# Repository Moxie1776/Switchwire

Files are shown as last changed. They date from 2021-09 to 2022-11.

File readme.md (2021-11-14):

# Voron Switchwire

<!-- ![Switchwire](./images/SWbedOn.jpg)  -->

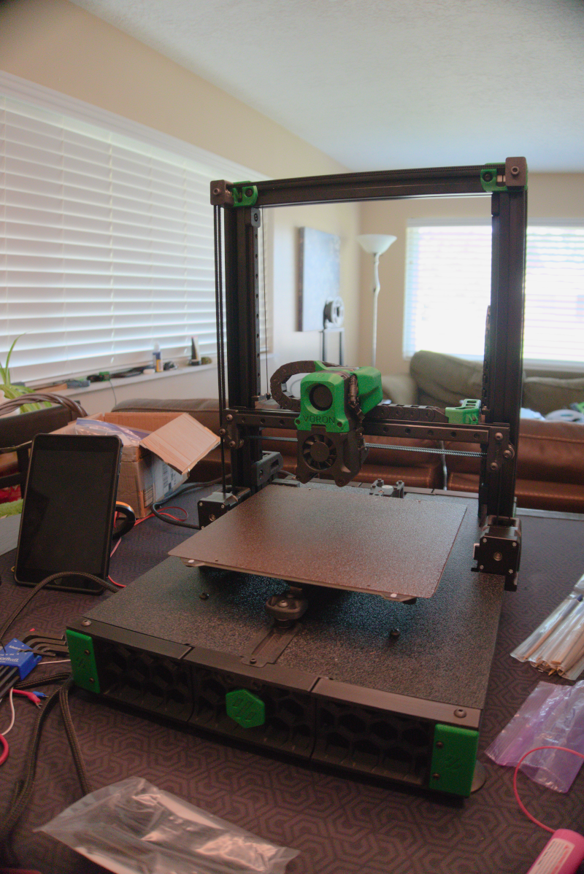
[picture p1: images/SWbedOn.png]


### BOM

-   Includes tax and S&H as much as was feasible
-   Due to my on hand parts some parts from the original BOM are not included

##### Printed Parts

-   Black Inland ABS
-   Green [KVP ABS](https://www.villageplastics.com/product/abs/)
-   printed FB friend (for a price)    
-   Black with Green accents

##### Fastners

-   [Fysetc Switchwire Fastner Set](https://www.aliexpress.com/item/1005002965204693.html) $37.66

##### Motion

-   [FYSETC GT2 Timing Belt](https://www.amazon.com/gp/product/B07BRKZGMS) $10.88
    -   [GATES-LL-2GT-6 Synchronous GT2](https://www.aliexpress.com/item/4001230715938.html) $31.79
    -   I have these on hand ready to put on
-   [POWGE 20 teeth 2GT Pulley Black Anodizing](https://www.aliexpress.com/item/4000454459268.html) $16.14
-   [Mellow F695-2RS Bearing 5_13_4 mm Flanged Bushing x2](https://www.aliexpress.com/item/1005001315513956.html) $20.38
-   [RobotDigg Black Anodized Linear Rails](https://www.robotdigg.com/product/1314/Black-anodized-linear-rail-7,-9,-12-and-15) $73.00
-   [Key-Bak](https://www.amazon.com/gp/product/B0088MQA10) $12.64

##### Vibration Management

-   [4 Rubber Compressor Feet](https://www.amazon.com/uxcell-47mmx18mm-Compressor-Replacement-Black/dp/B0711Y6T56) $9.99

##### Electronics

-   [Limit Switches](https://www.digikey.com/en/products/detail/omron-electronics-inc-emc-div/D2F-5L/8593137) $17.58
-   [Omron Proximity Switch Inductive Sensor 3 Wire](https://www.aliexpress.com/item/32442790824.html) $18.78
-   Bat-85 Diode not needed with the Fysetc S6
-   [Mean Well RS-25-5](https://www.digikey.com/en/products/detail/RS-25-5/1866-4145-ND/7706180) $11.54 ($4.99 S&H)
-   [NEMA17 Motor 17HS15-1504S-X1 x3](https://www.amazon.com/gp/product/B07LCK19D5) $30.22
-   [NEMA17 Motor 17HS08-1004S x3](https://www.amazon.com/gp/product/B00PNEQ79Q) $11.79
-   Mean Well LRS-350-24 PSU - recycled from Ender 3

-   [Filtered Power Inlet](https://www.amazon.com/gp/product/B081VD1NNT) $11.79
-   [40x40x10 Axial Fan 24V](https://www.aliexpress.com/item/32815685199.html) $4.65
-   [40x40x20 Blower Fan 24V](https://www.aliexpress.com/item/4001246935816.html) $5.06
-   60x60x20 Axial Fan (24V) - recycled from Ender 3 (upgraded PSU fan from original PSU)
-   [Raspberry Pi 4 Model B/4GB](https://www.pishop.us/product/raspberry-pi-4-model-b-4gb/) - recycled from Ender 3
-   [Fysetc S6 V2](https://www.aliexpress.com/item/4000345369228.html)
    -   [Fysetc TMC2209 v3.1 x 5](https://www.aliexpress.com/item/33025556705.html)

##### Frame

-   [LDO Frame](https://www.printedsolid.com/products/ldo-voron-switchwire-frame-kit) $95.00

##### Misc

-   [Neodymium Rare Earth Magnets 6x3mm 70pcs, Black](https://www.amazon.com/gp/product/B00HA2LM30) $16.99
-   [Mellow BMG Extruder Kit](https://www.aliexpress.com/item/1005002254569027.html) $25.61
-   [Mellow All Metal NF V6-Crazy Voron Hotend E3d V6](https://www.aliexpress.com/item/4001230851527.html) $33.67
-   [ Hook Up Wire, 24 AWG, Stranded Kit](https://www.remingtonindustries.com/hook-up-wire/custom-hook-up-wire-24-awg-stranded-kit-25-length-each-choose-6-colors/) $22.82
-   [10\*11mm Mini Nylon Drag Chain](https://www.aliexpress.com/item/33000014666.html) $19.99

##### Panels/Build Plate

-   [Prusa i3 MK3S Y carriage compatible with Voron Switchwire](https://www.aliexpress.com/item/4000046376872.html) $31.96
-   [Prusa I3 MK3 MK52 Heated Bed + Double Sided Textured Powder Coated PEI Spring Steel Sheet For VORON SW](https://www.aliexpress.com/item/4000016762364.html) $61.73
-   [Laser Cut ABS Deck, Enclosure (minus clear)](https://mnlasercutting.com/shop/voron-switchwire) $45.00
-   [Clear Acrylic Enclosure Parts](https://www.printedsolid.com/products/voron-switchwire-panel-set-made-from-aluminum-composite-material) $34.00
    -   I would have just purchased the entire enclosure set from printedsolid 'had a known'

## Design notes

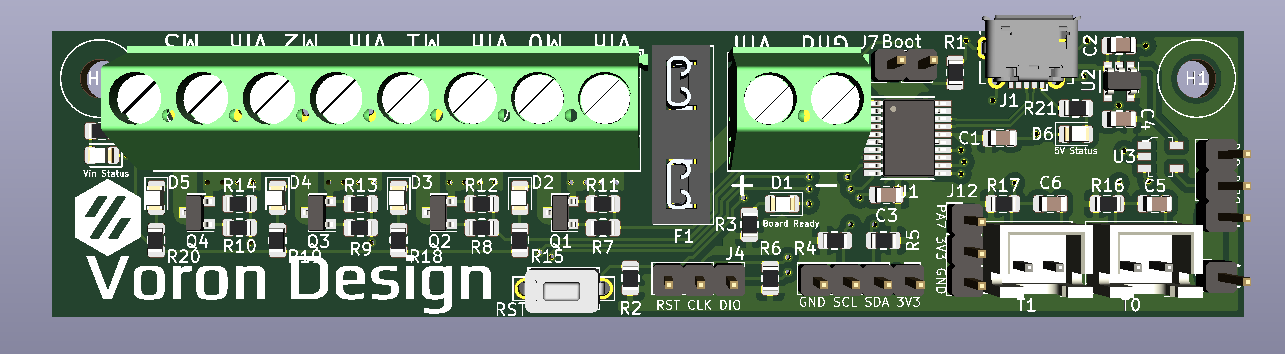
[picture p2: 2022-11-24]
electronics/Klipper_Expander/Images/STM32_Klipper_Expander.png

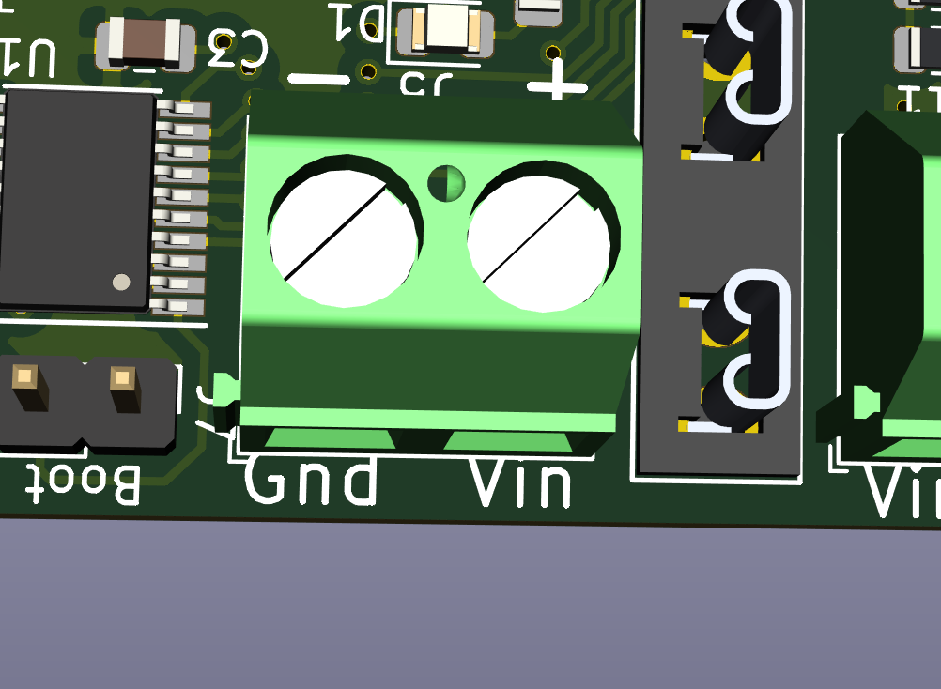
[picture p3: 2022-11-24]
electronics/Klipper_Expander/Images/Vin.png

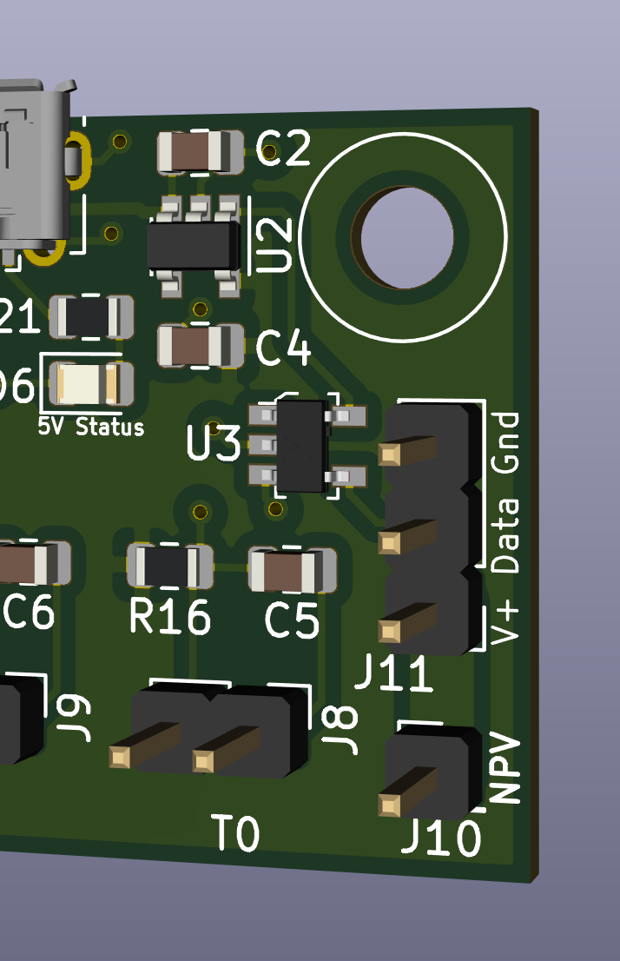
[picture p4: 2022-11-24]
electronics/Klipper_Expander/Images/Neopixel.png

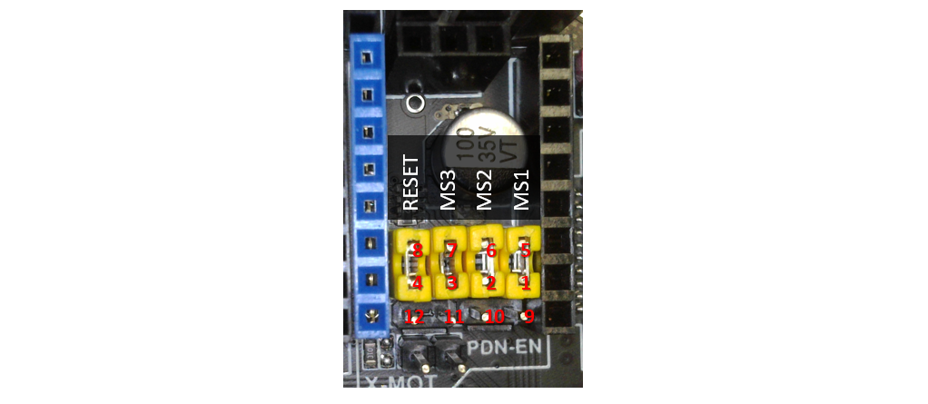
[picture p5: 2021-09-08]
electronics/FYSETC-S6-main/images/S6_1574477723736.png

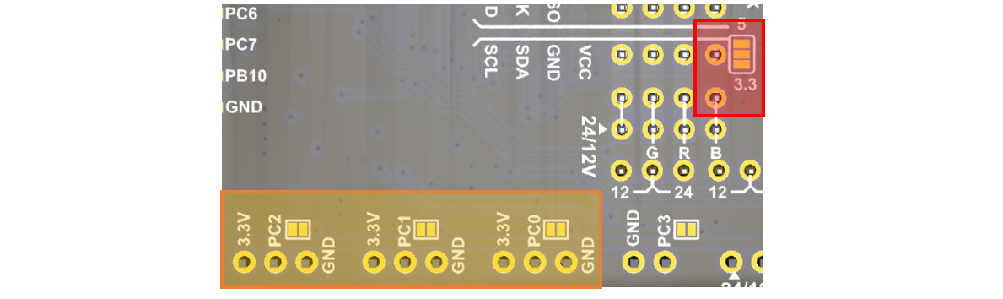
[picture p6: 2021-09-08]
electronics/FYSETC-S6-main/images/S6_1574476533464.png

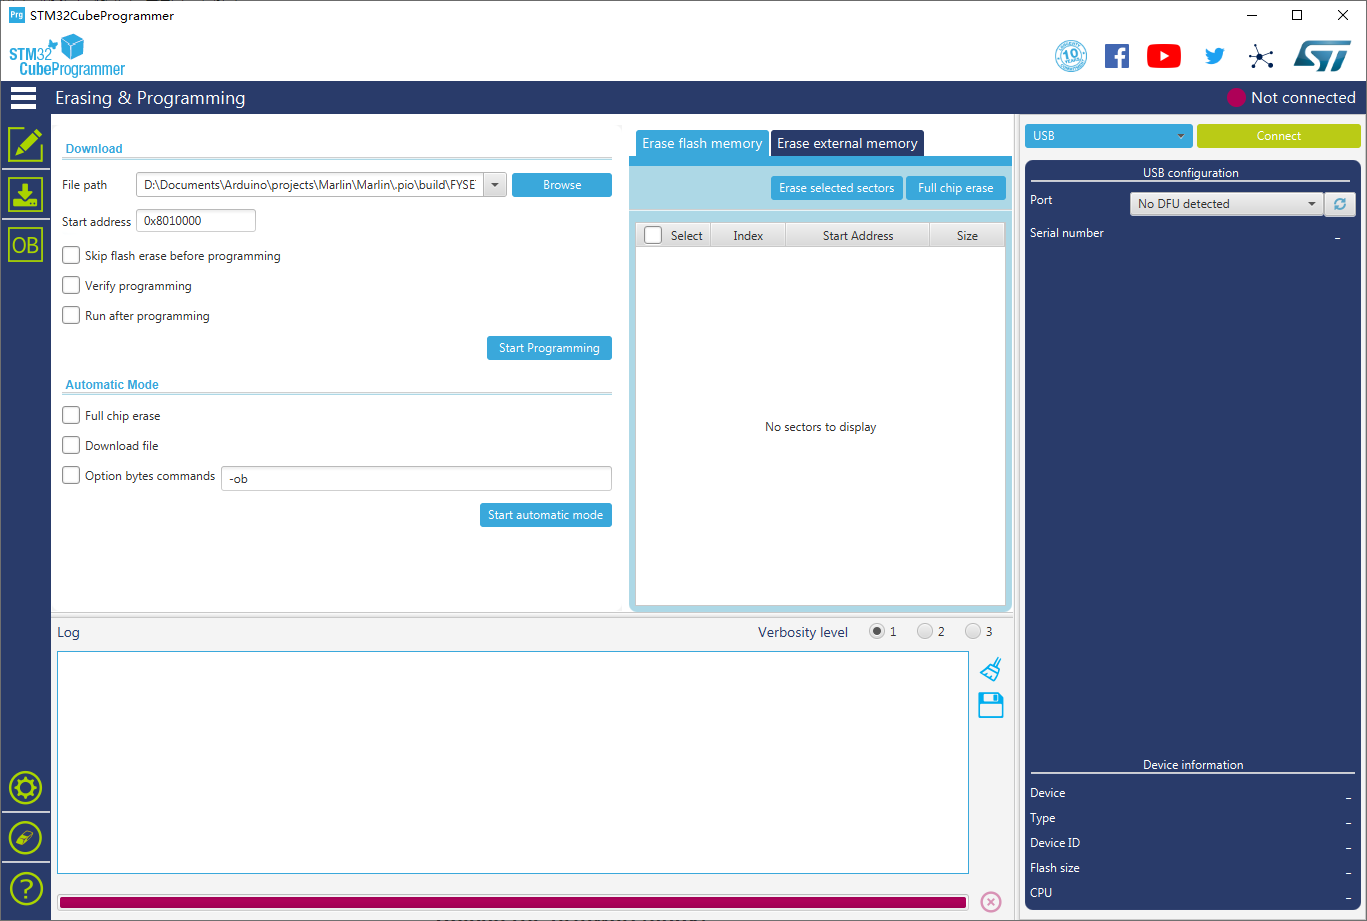
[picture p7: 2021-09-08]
electronics/FYSETC-S6-main/bootloader/images/STM32CubeProgrammer.png

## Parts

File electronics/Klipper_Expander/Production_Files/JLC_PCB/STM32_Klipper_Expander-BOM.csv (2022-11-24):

Comment | Designator | Footprint | LCSC
0.1uF | C1,C3 | KlipperExpander:C_0805_2012Metric | C49678
4.7uF | C4,C2,C5,C6 | KlipperExpander:C_0805_2012Metric | C1779
LED | D1,D2,D4,D3,D5,D7,D6 | KlipperExpander:LED_0805_2012Metric | C84256
Fuse | F1 | KlipperExpander:3544-2_FuseHolder
MountingHole | H1,H2 | KlipperExpander:MountingHole_3.2mm_M3
USB_B_Micro | J1 | KlipperExpander:Molex-105017-0001-USBMicroB
Conn_01x01 | J10 | KlipperExpander:PinHeader_1x01_P2.54mm_Vertical
Conn_01x03 | J11,J12,J4 | KlipperExpander:PinHeader_1x03_P2.54mm_Vertical
Conn_01x04 | J2 | KlipperExpander:PinHeader_1x04_P2.54mm_Vertical
Vin | J5 | KlipperExpander:1x02_ScrewTerminal_Phoenix
Screw_Terminal_01x08 | J6 | KlipperExpander:1x08_ScrewTerminal_Phoenix
Conn_01x02 | J7,J8,J9 | KlipperExpander:PinHeader_1x02_P2.54mm_Vertical
IRLML6344TRPBF | Q1,Q3,Q2,Q4 | KlipperExpander:SOT-23 | C20917
10K | R2,R1,R13,R12,R11,R6,R14 | KlipperExpander:R_0805_2012Metric | C17414
1K | R3,R21 | KlipperExpander:R_0805_2012Metric | C17513
4.7K | R5,R4,R15,R19,R18,R20,R22,R16,R17 | KlipperExpander:R_0805_2012Metric | C17673
100 | R7,R8,R9,R10 | KlipperExpander:R_0805_2012Metric | C17408
SW_SPST | SW2 | KlipperExpander:2PinTactileButton
STM32F042F6Px | U1 | KlipperExpander:TSSOP-20_4.4x6.5mm_P0.65mm | C81000
AP2127K-3.3 | U2 | KlipperExpander:SOT-23-5 | C156285
74LVC1G17 | U3 | KlipperExpander:SOT-753 | C6076

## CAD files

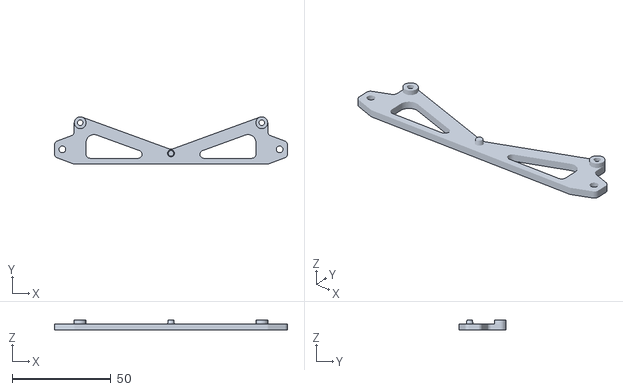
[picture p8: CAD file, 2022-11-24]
electronics/Klipper_Expander/CAD/KlipperExpander_HorizontalMount.STL
118.0 x 24.0 x 5.00

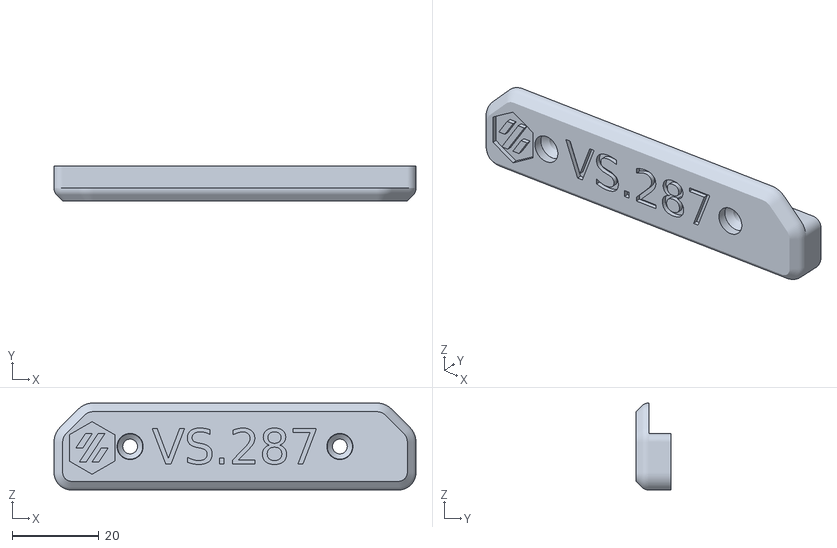
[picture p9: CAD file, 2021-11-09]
serialFiles/VS.287.stl
83.2 x 8.00 x 20.0

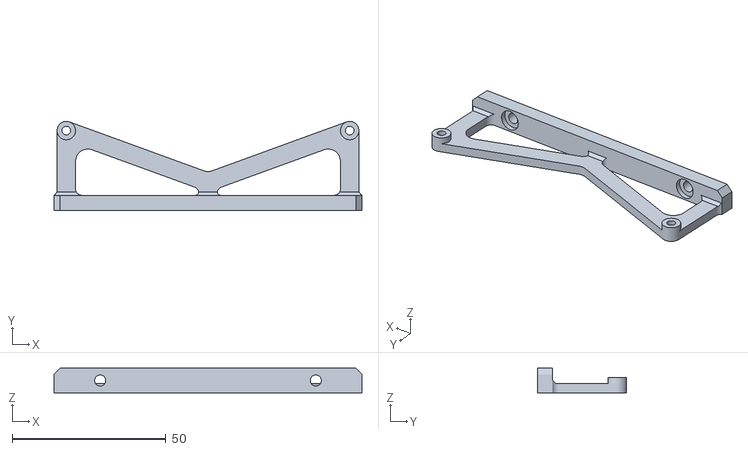
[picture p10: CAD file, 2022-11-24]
electronics/Klipper_Expander/CAD/KlipperExpander_VerticalMount.STL
100.0 x 29.0 x 8.00

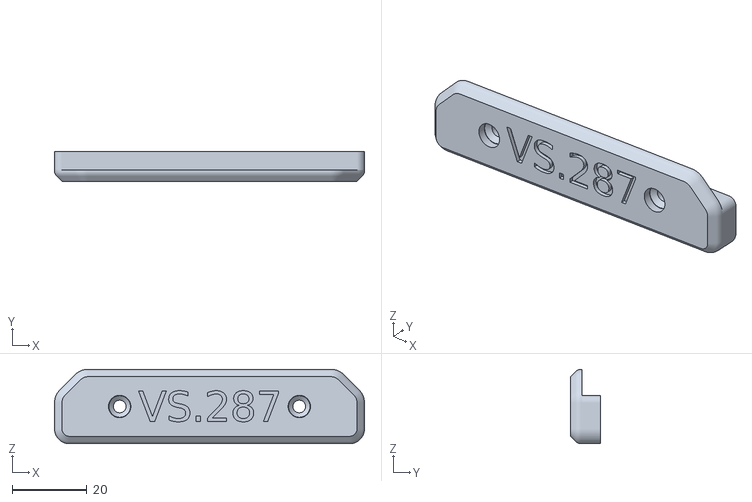
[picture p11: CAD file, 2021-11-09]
serialFiles/VS.287-NoLogo.stl
83.2 x 8.00 x 20.0

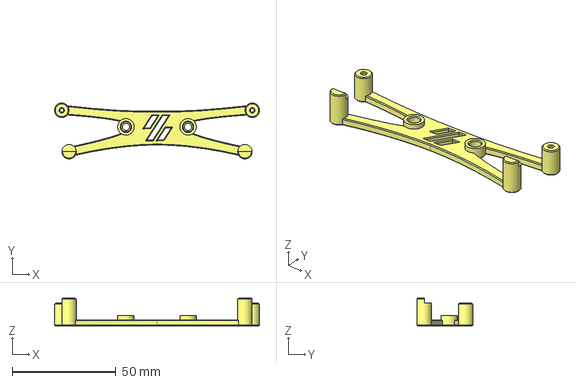
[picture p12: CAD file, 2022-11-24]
electronics/Klipper_Expander/CAD/KlipperExpander_RailMount.step
99.0 x 27.0 x 13.5 mm

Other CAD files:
electronics/Klipper_Expander/CAD/KlipperExpander_RailMount.stl

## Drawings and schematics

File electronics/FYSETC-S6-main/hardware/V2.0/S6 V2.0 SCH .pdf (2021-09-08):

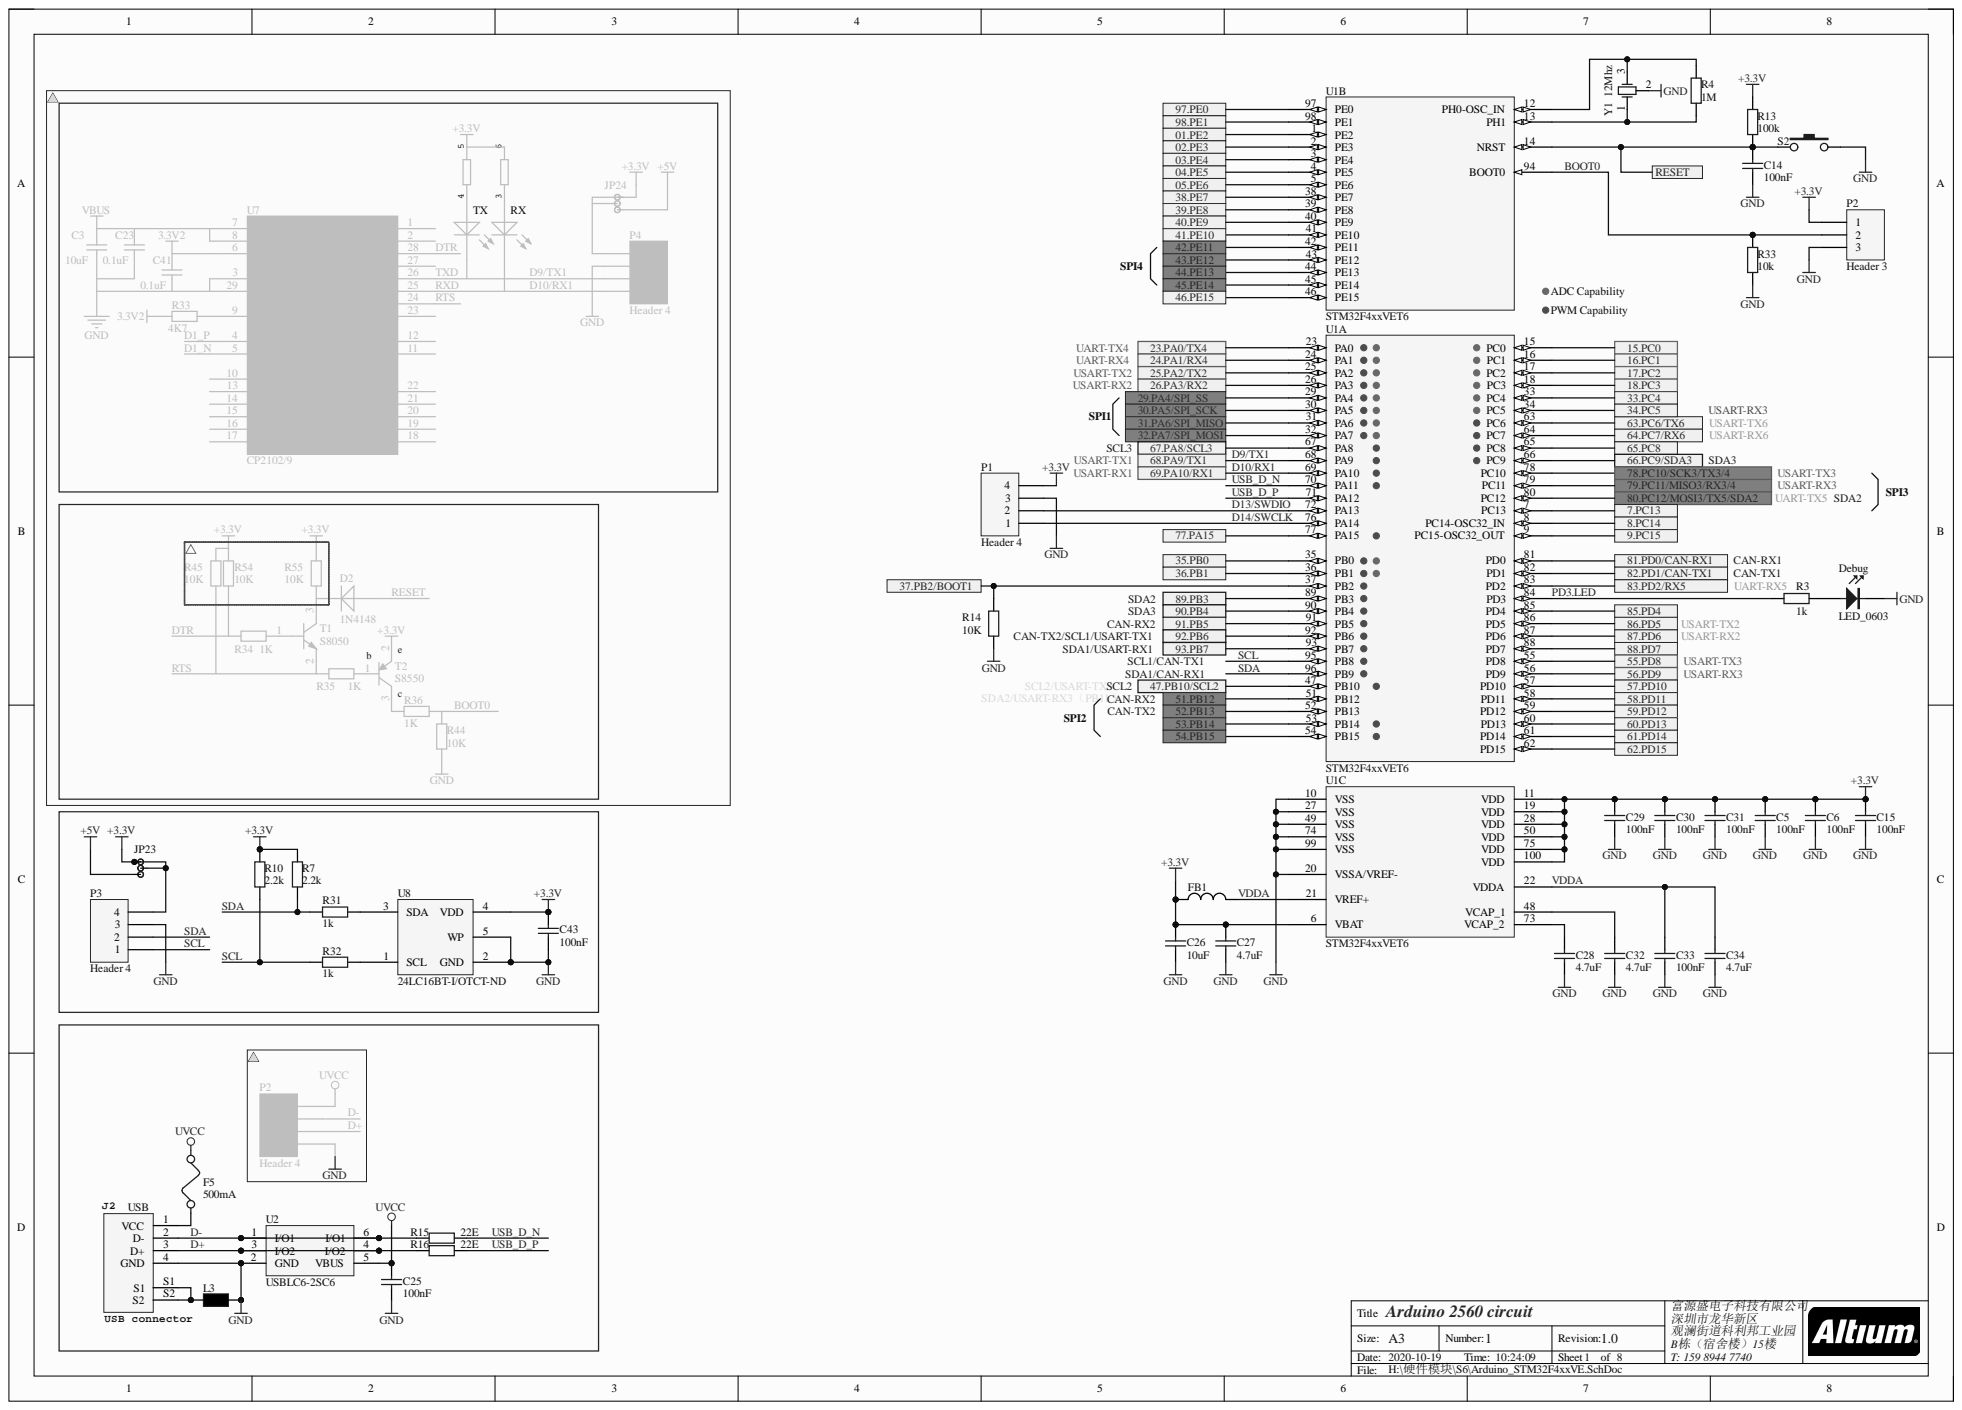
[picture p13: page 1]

01.PE2 | PE2 1
02.PE3 | PE4 3 | BOOT0

05.PE6 | PE7 38
38.PE7 | PE8 39

32.PA7/SPI_MOSI | | 64.PC7/RX6
67.PA8/SCL3 | PA8 67 | 65.PC8

35.PB0 | | PB1 36 | | 81.PD0/CAN-RX1
36.PB1 | | | | 82.PD1/CAN-TX1

89.PB3 | PB4 90
91.PB5 | | PB5 91 | | 86.PD5
92.PB6 | | PB6 92 | | 87.PD6
93.PB7 | SCL | PB8 95 | | 88.PD7

47.PB10/SCL2 | PB12 51 | 57.PD10
51.PB12 | PB13 52 | 58.PD11
52.PB13 | | 59.PD12
53.PB14 | PB14 53 | 60.PD13
54.PB15 | | 61.PD14

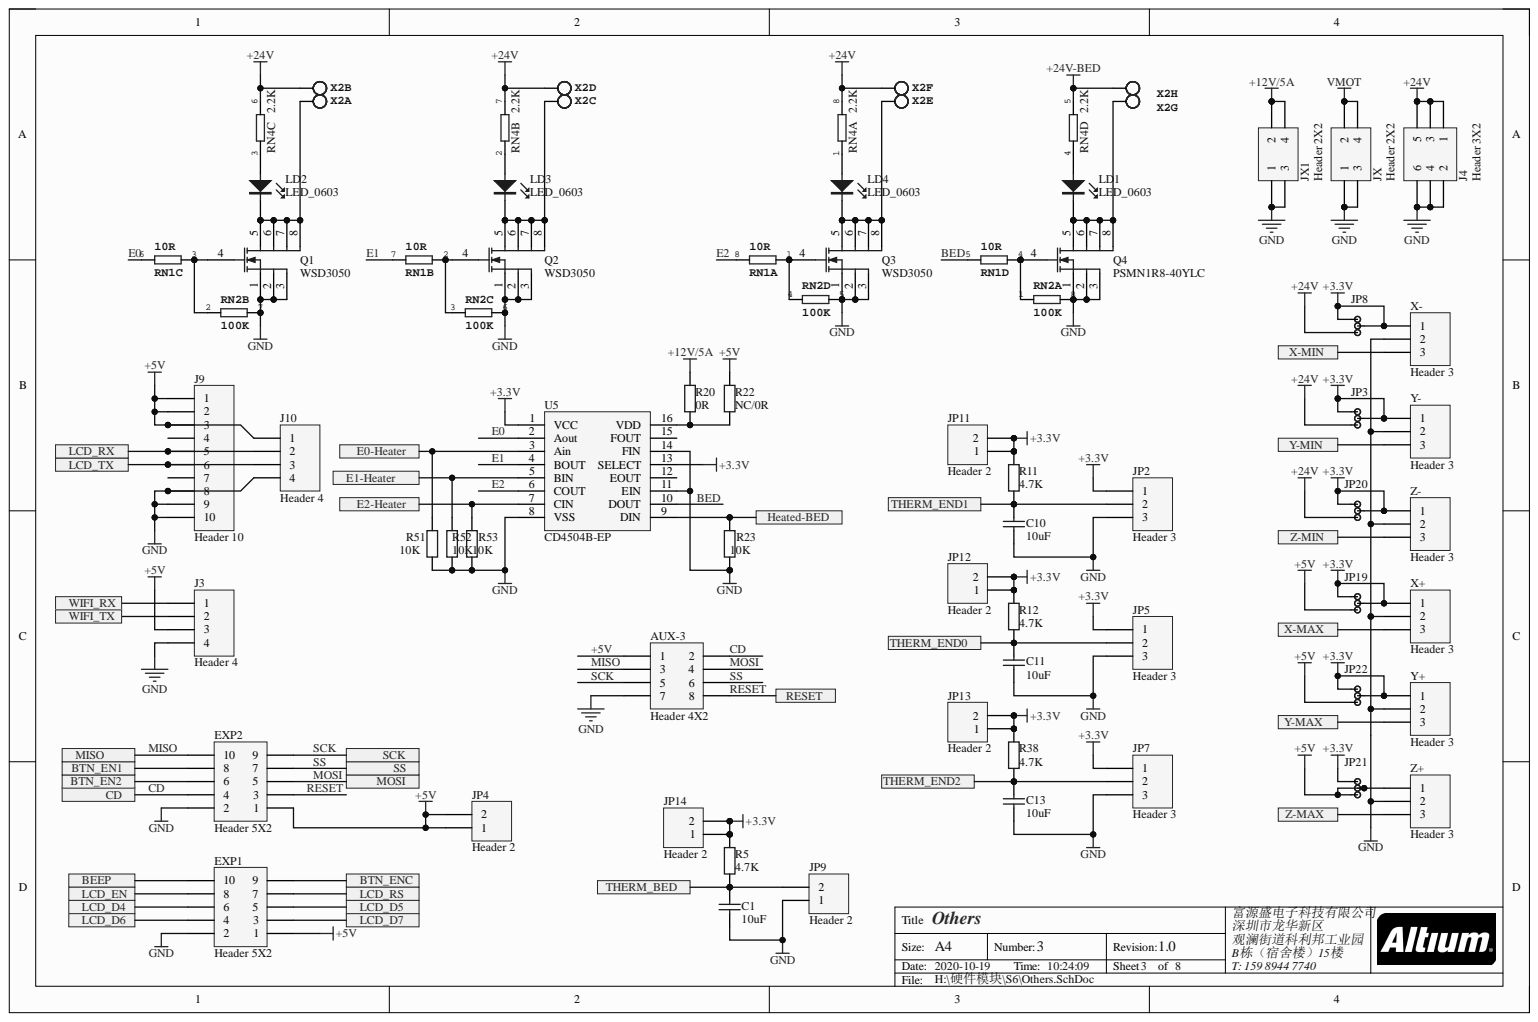
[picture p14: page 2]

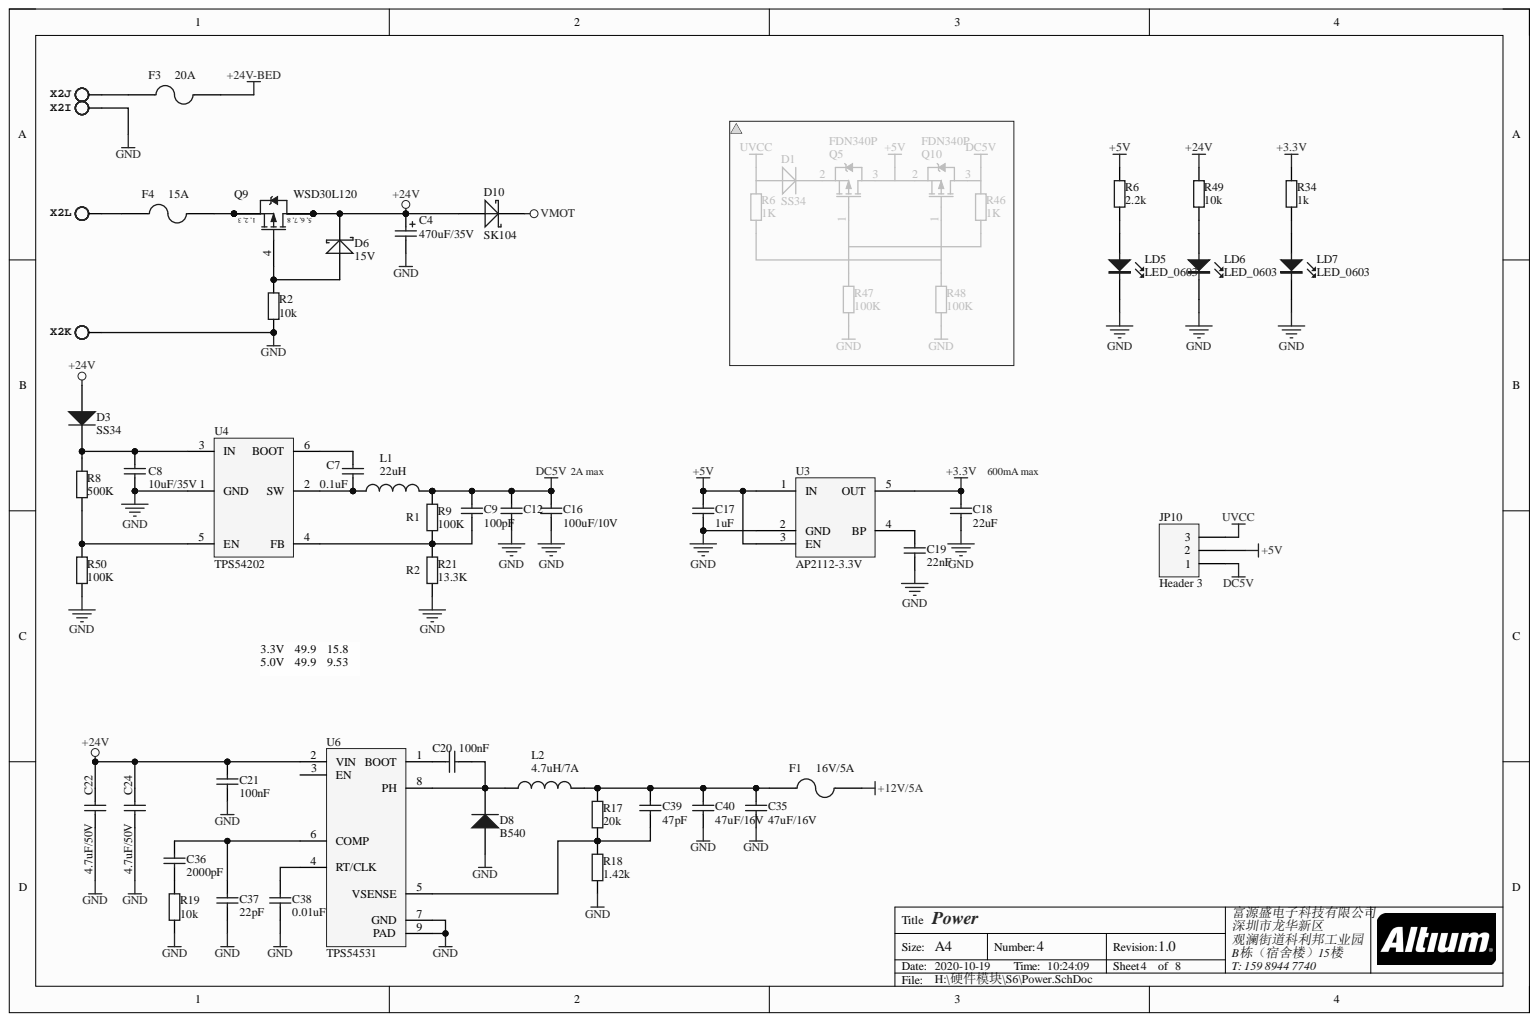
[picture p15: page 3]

RT/CLK 4

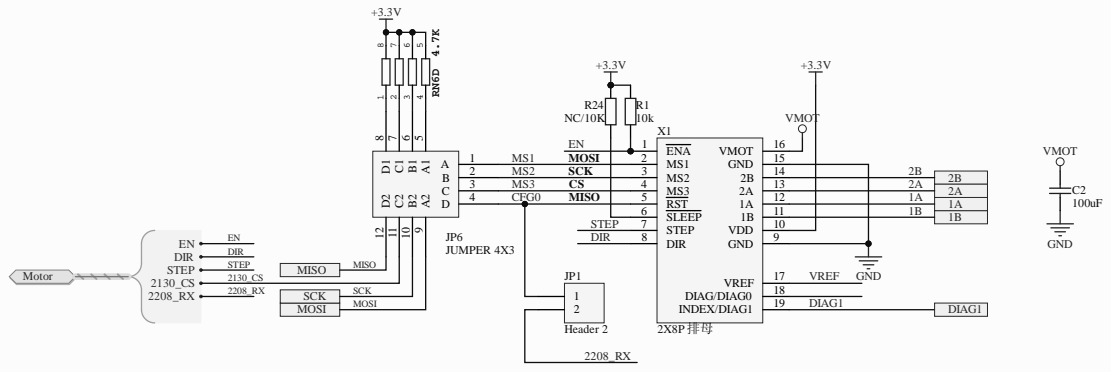
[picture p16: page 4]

2 MS2 SC K | 3 | 1 4
3 MS3 C S | 4 | 1 3 | | 2 A
4 CFG 0 ISO M | 5 | 1 2 | | 1 A

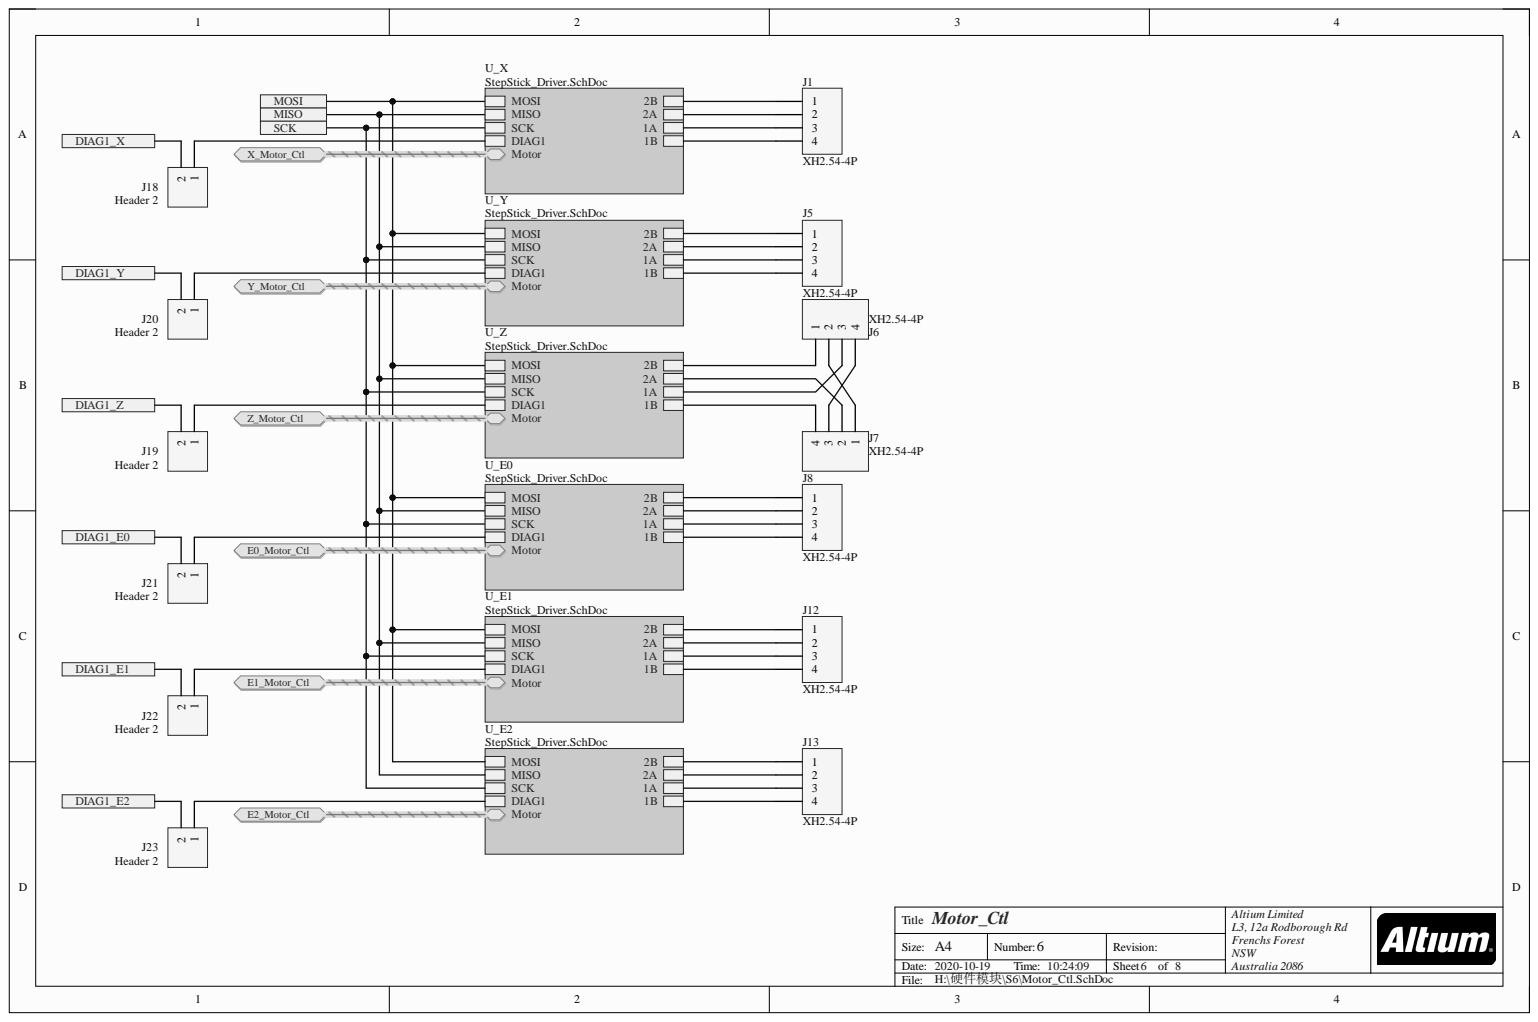
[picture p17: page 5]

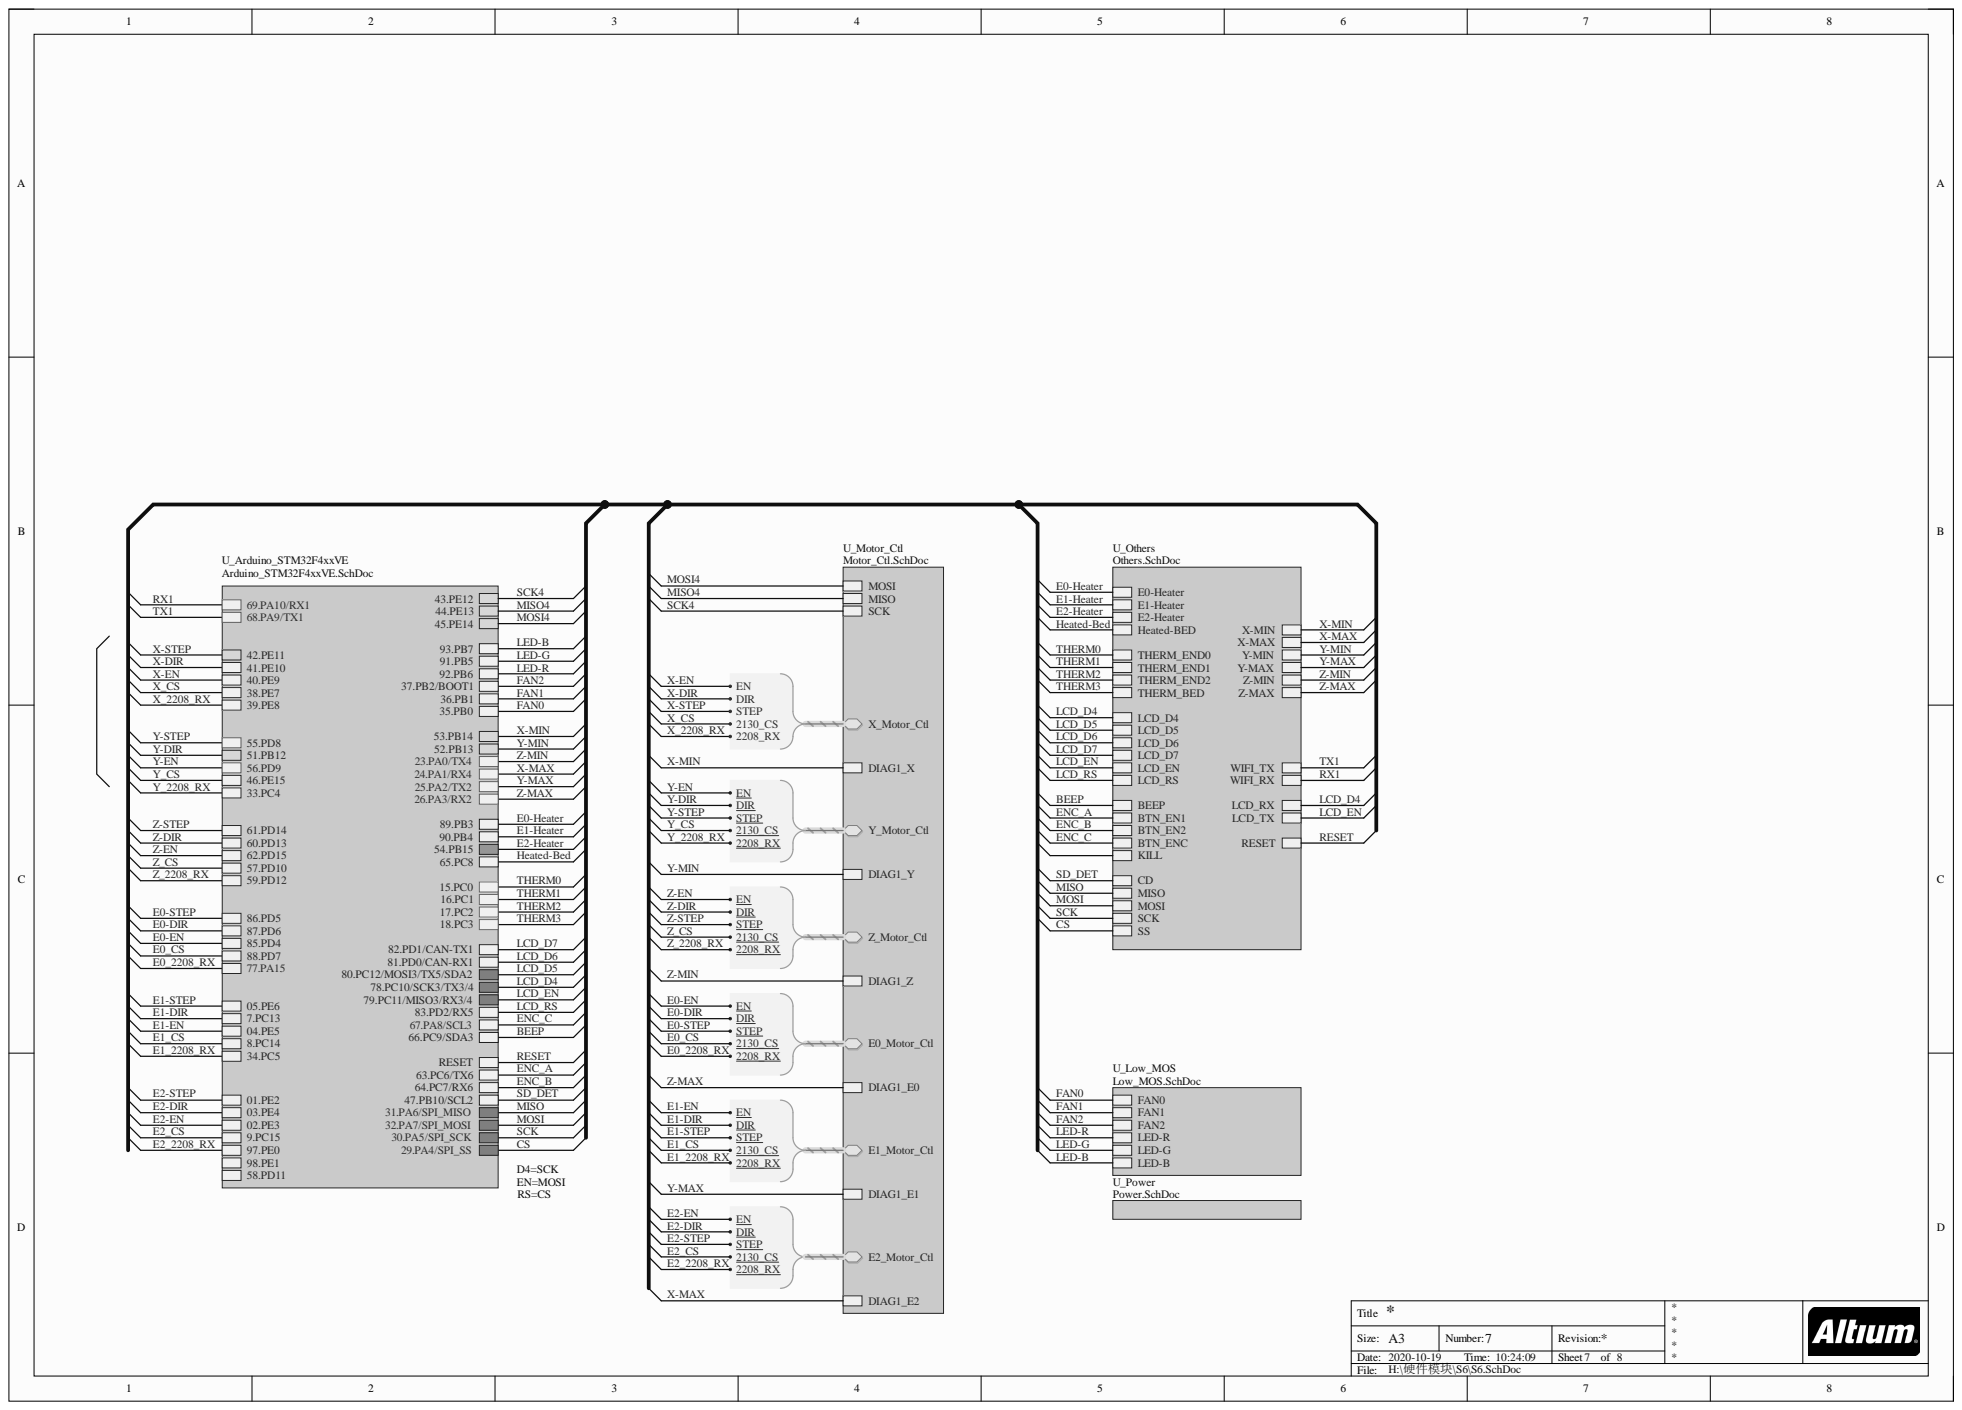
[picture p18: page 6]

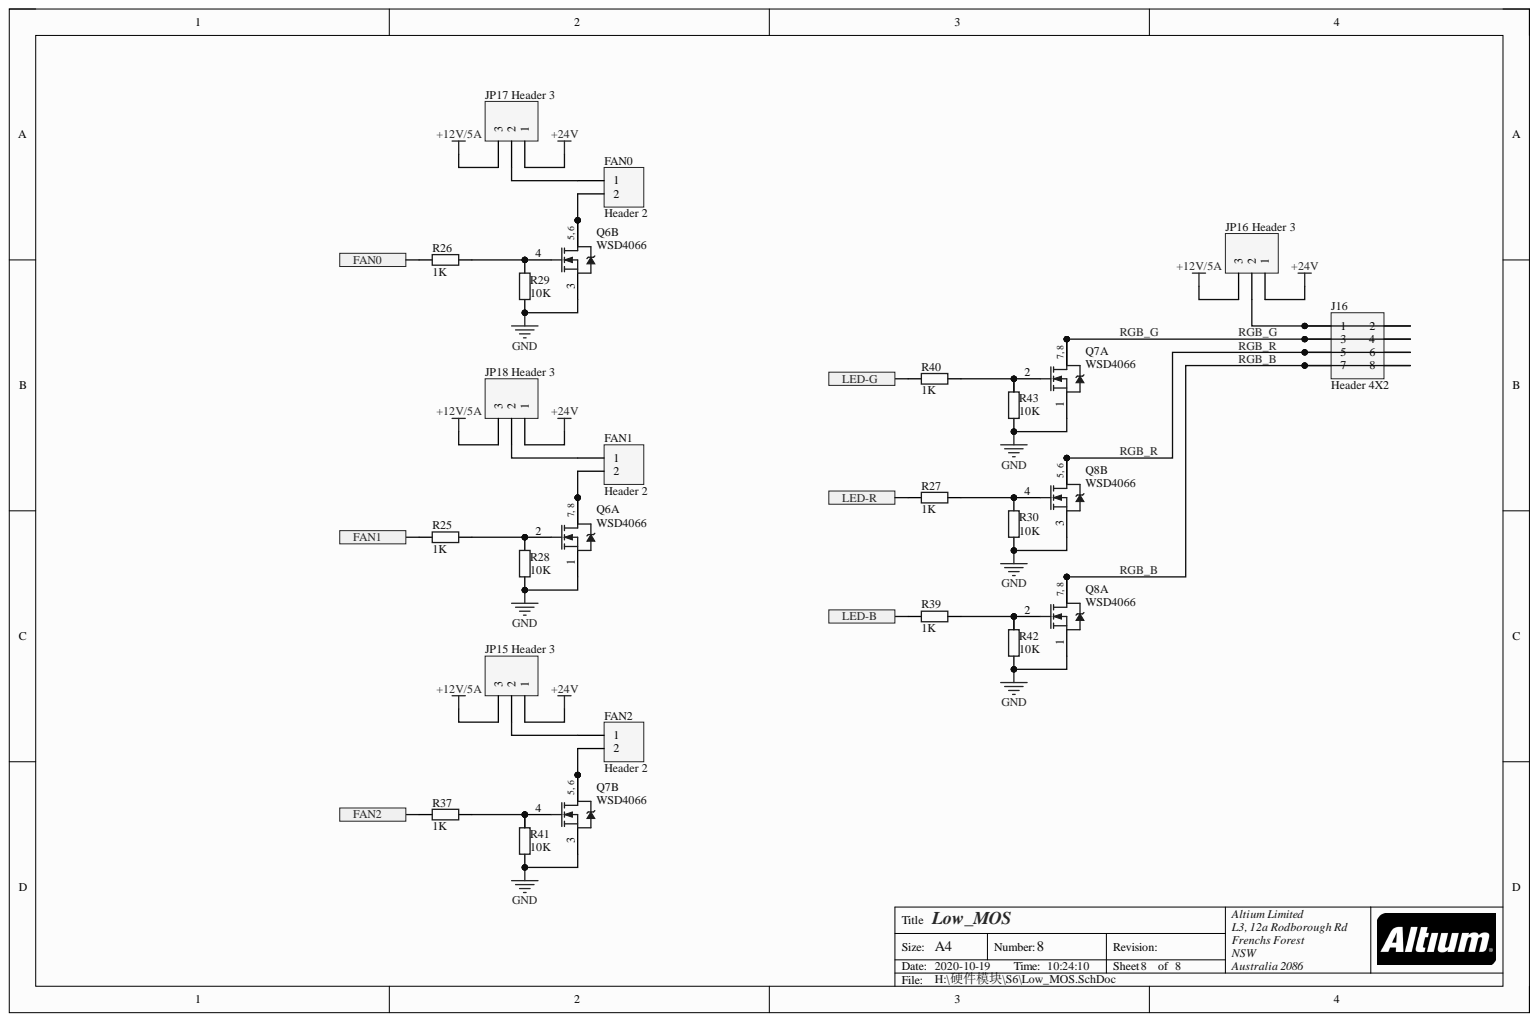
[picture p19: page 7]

RGB_ R Q 7 A | 5 6

RGB_ B | 7 8

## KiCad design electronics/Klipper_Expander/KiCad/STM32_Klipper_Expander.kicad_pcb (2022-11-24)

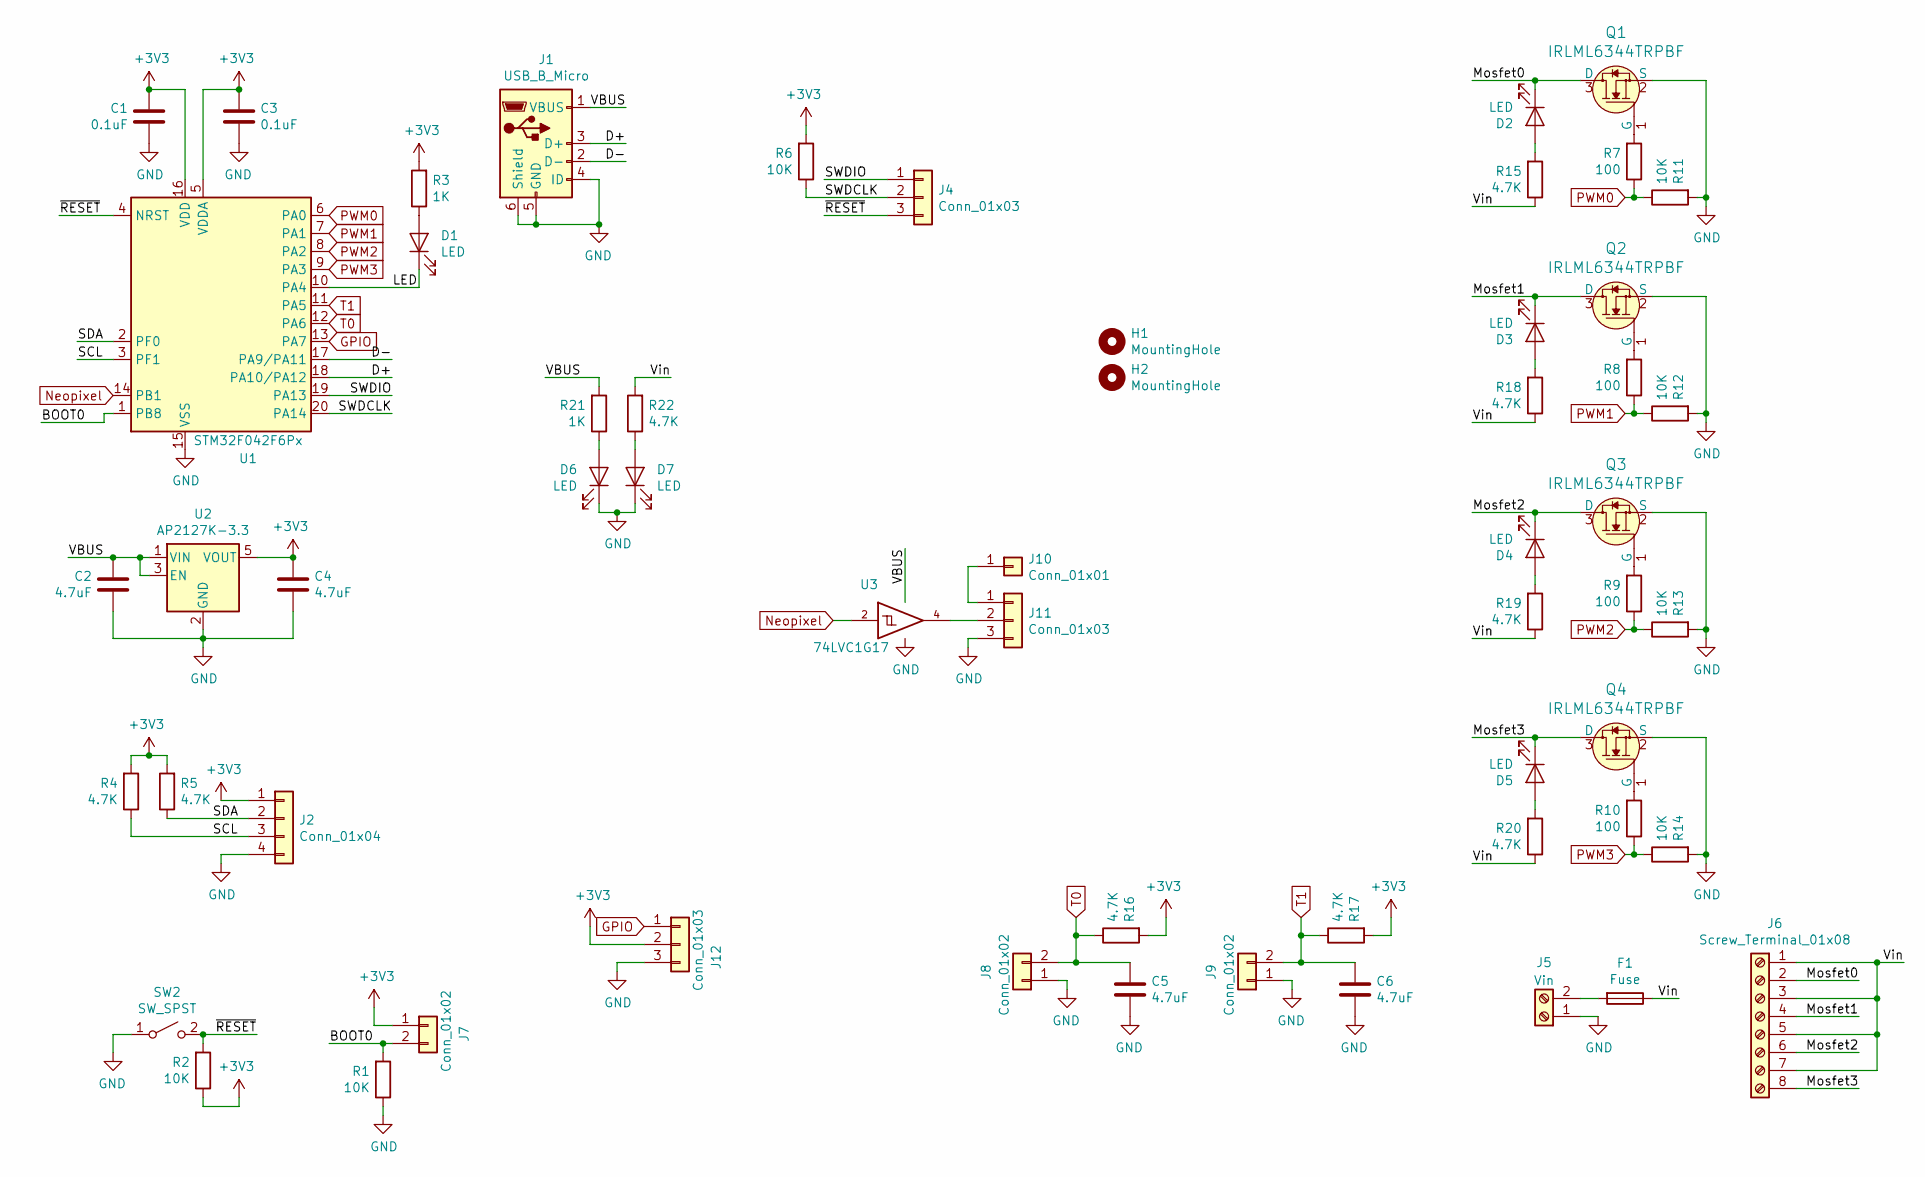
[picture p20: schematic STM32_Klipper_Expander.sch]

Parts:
C1, C3: 0.1uF; C_0805_2012Metric; MPN CC0805KRX7R9BB104; LCSC C49678
C2, C4, C5, C6: 4.7uF; C_0805_2012Metric; MPN CC0805KKX5R8BB475; LCSC C1779
D1, D2, D3, D4, D5, D6, D7: LED; LED_0805_2012Metric; MPN 17-215SURC/S530-A2/TR8; LCSC C84256
F1: Fuse; 3544-2_FuseHolder
H1, H2: MountingHole; MountingHole_3.2mm_M3
J1: USB_B_Micro; Molex-105017-0001-USBMicroB; MPN 1050170001
J2: Conn_01x04; PinHeader_1x04_P2.54mm_Vertical
J4, J11, J12: Conn_01x03; PinHeader_1x03_P2.54mm_Vertical
J5: Vin; 1x02_ScrewTerminal_Phoenix
J6: Screw_Terminal_01x08; 1x08_ScrewTerminal_Phoenix
J7, J8, J9: Conn_01x02; PinHeader_1x02_P2.54mm_Vertical
J10: Conn_01x01; PinHeader_1x01_P2.54mm_Vertical
Q1, Q2, Q3, Q4: IRLML6344TRPBF; SOT-23; MPN IRLML6344TRPBF; Digi-Key_PN IRLML6344TRPBFCT-ND
R1, R2, R6, R11, R12, R13, R14: 10K; R_0805_2012Metric; MPN RC0805JR-0710KL; LCSC C17414
R3, R21: 1K; R_0805_2012Metric; MPN RC0805JR-071KL; LCSC C17513
R4, R5, R15, R16, R17, R18, R19, R20, R22: 4.7K; R_0805_2012Metric; MPN RC0805JR-074K7L; LCSC C17673
R7, R8, R9, R10: 100; R_0805_2012Metric; MPN RC0805JR-07100RL; LCSC C17408
SW2: SW_SPST; 2PinTactileButton
U1: STM32F042F6Px; TSSOP-20_4.4x6.5mm_P0.65mm; MPN STM32F042F6P6; LCSC C81000
U2: AP2127K-3.3; SOT-23-5; MPN AP2127K-3.3TRG1; LCSC C156285
U3: 74LVC1G17; SOT-753; LCSC C6076

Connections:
+3V3: C1.2, C3.2, C4.2, J2.1, J7.1, J12.2, R2.1, R3.2, R4.2, R5.2, R6.2, R16.2, R17.2, U1.5 (VDDA), U1.16 (VDD), U2.5 (VOUT)
/BOOT0: J7.2, R1.2, U1.1 (PB8)
/D+: J1.3 (D+), U1.18 (PA10/PA12)
/D-: J1.2 (D-), U1.17 (PA9/PA11)
/LED: D1.1 (K), U1.10 (PA4)
/Mosfet0: D2.1 (K), J6.2, Q1.3 (D)
/Mosfet1: D3.1 (K), J6.4, Q2.3 (D)
/Mosfet2: D4.1 (K), J6.6, Q3.3 (D)
/Mosfet3: D5.1 (K), J6.8, Q4.3 (D)
/SCL: J2.3, R4.1, U1.3 (PF1)
/SDA: J2.2, R5.1, U1.2 (PF0)
/SWDCLK: J4.2, R6.1, U1.20 (PA14)
/SWDIO: J4.1, U1.19 (PA13)
/Vin: F1.1, J6.1, J6.3, J6.5, J6.7, R15.1, R18.1, R19.1, R20.1, R22.2
/~RESET: J4.3, R2.2, SW2.2 (B), U1.4 (NRST)
GND: C1.1, C2.1, C3.1, C4.1, C5.1, C6.1, D6.1 (K), D7.1 (K), J1.4 (ID), J1.5 (GND), J1.6 (Shield), J2.4, J5.1, J8.1, J9.1, J11.3, J12.3, Q1.2 (S), Q2.2 (S), Q3.2 (S), Q4.2 (S), R1.1, R11.2, R12.2, R13.2, R14.2, SW2.1 (A), U1.15 (VSS), U2.2 (GND), U3.3 (GND)
GPIO: J12.1, U1.13 (PA7)
Neopixel: U1.14 (PB1), U3.2
unnamed: D1.2 (A), R3.1
unnamed: D2.2 (A), R15.2
unnamed: D3.2 (A), R18.2
unnamed: D4.2 (A), R19.2
unnamed: D5.2 (A), R20.2
unnamed: D6.2 (A), R21.1
unnamed: D7.2 (A), R22.1
unnamed: F1.2, J5.2
unnamed: J10.1, J11.1
unnamed: J11.2, U3.4
unnamed: Q1.1 (G), R7.2
unnamed: Q2.1 (G), R8.2
unnamed: Q3.1 (G), R9.2
unnamed: Q4.1 (G), R10.2
PWM0: R7.1, R11.1, U1.6 (PA0)
PWM1: R8.1, R12.1, U1.7 (PA1)
PWM2: R9.1, R13.1, U1.8 (PA2)
PWM3: R10.1, R14.1, U1.9 (PA3)
T0: C5.2, J8.2, R16.1, U1.12 (PA6)
T1: C6.2, J9.2, R17.1, U1.11 (PA5)
VCC: C2.2, J1.1 (VBUS), R21.2, U2.1 (VIN), U2.3 (EN), U3.5 (VCC)

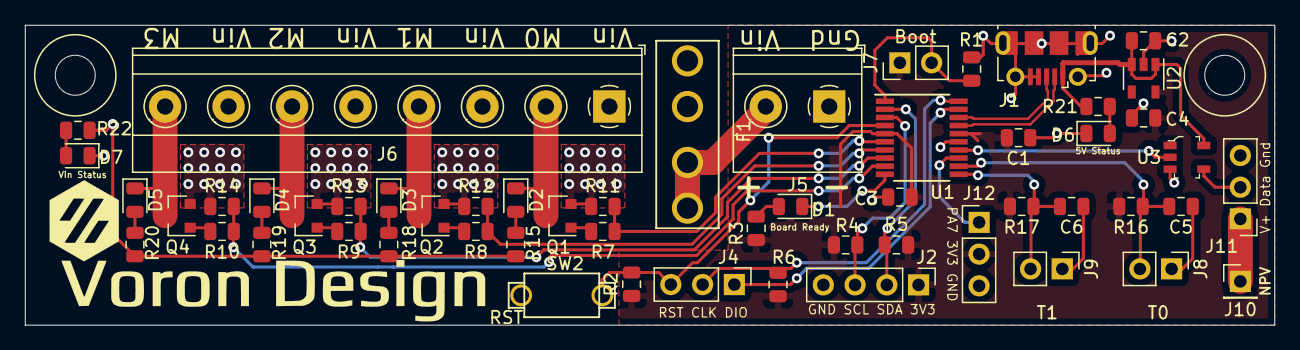
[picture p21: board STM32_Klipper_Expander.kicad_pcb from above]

Board: 2 copper layers, 100.0 x 24.0 mm, 57 parts (0 on the bottom side), 39 nets.

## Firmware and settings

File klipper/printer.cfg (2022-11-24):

# Fysetc S6 V2
# 64KiB bootloader
# extra low-level configuration
#   clock reference 12MHz crystal
# make flash FLASH_DEVICE=/dev/serial/by-id/usb-Klipper_stm32f446xx_36005A000851363131363530-if00

# scp pi@192.168.0.34:/home/pi/klipper_config/*.cfg $HOME/Downloads/
# scp pi@192.168.0.34:/home/pi/.moonraker_database/* $HOME/Downloads/


[include macros.cfg]
# [include neopixel_macros.cfg]

# open
# [input_shaper]
# shaper_freq_x: 57.2
# shaper_type_x: mzv
# shaper_freq_y: 50.0
# shaper_type_y: mzv

# enclosed
# [input_shaper]
# shaper_freq_x: 34.2
# shaper_type_x: mzv
# shaper_freq_y: 31.2
# shaper_type_y: mzv

[printer]
kinematics: corexz
max_velocity: 250
max_accel: 2500
max_z_velocity: 125
max_z_accel: 2500
# square_corner_velocity: 6.0

[mcu]
serial: /dev/serial/by-id/usb-Klipper_stm32f446xx_3D001B000951363131363530-if00

[mcu rpi]
serial: /tmp/klipper_host_mcu

# [adxl345]
# cs_pin: rpi:None

# [resonance_tester]
# accel_chip: adxl345
# probe_points:
#     121,125,40  # an example


[output_pin caselight]
pin: PB5
# pwm: True

[respond] # enable RESPOND and M118 sens msg to local display

#################################################################
#     X/Y Stepper Settings
#################################################################

[stepper_x]
step_pin: PE11
dir_pin: !PE10
enable_pin: !PE9
rotation_distance: 40
microsteps: 32
full_steps_per_rotation: 200
endstop_pin: ^PB14 
position_endstop: 250
position_min: 0
position_max: 250
homing_speed: 150
homing_positive_dir: true

[tmc2209 stepper_x]
uart_pin: PE8
run_current: 0.8
hold_current: 0.5
stealthchop_threshold: 0

[stepper_y]
step_pin: PD8
dir_pin: !PB12
enable_pin: !PD9
rotation_distance: 40
microsteps: 32
full_steps_per_rotation: 200
endstop_pin: ^PB13  
position_endstop: 250
position_min: 0
position_max: 250
homing_speed: 150
homing_positive_dir: true

[tmc2209 stepper_y]
uart_pin: PC4
run_current: 0.8
hold_current: 0.5
stealthchop_threshold: 0

#####################################################################
#     Z/E Stepper Settings
#####################################################################

[stepper_z]
step_pin: PD14
dir_pin: !PD13
enable_pin: !PD15
rotation_distance: 40
microsteps: 32
full_steps_per_rotation: 200
endstop_pin: probe:z_virtual_endstop
position_max: 250
homing_speed: 50
position_min: -5.0

[tmc2209 stepper_z]
uart_pin: PD12
run_current: 0.8
hold_current: 0.5
stealthchop_threshold: 0

[extruder]
step_pin: PD5
dir_pin: !PD6
enable_pin: !PD4
rotation_distance: 22.6789511
gear_ratio: 50:17
microsteps: 32
full_steps_per_rotation: 200
# pressure_advance: .054 # SunLu PLA+
pressure_advance: .074
nozzle_diameter: 0.400
filament_diameter: 1.750
heater_pin: PB3
# sensor_type: NTC 100K beta 3950
sensor_type: Custom NTC100K B3950
sensor_pin: PC0
#control: pid
#pid_Kp: 22
#pid_Ki: 1.08
#pid_Kd: 114
min_temp: -75
max_temp: 270

[tmc2209 extruder]
uart_pin: PA15
run_current: 0.6
hold_current: 0.3
stealthchop_threshold: 0

[thermistor Custom NTC100K B3950]
## values calibrated against a PT100 reference
temperature1: 25.0
resistance1: 103180.0
temperature2: 150.0
resistance2: 1366.2
temperature3: 250.0
resistance3: 168.6

[homing_override]
axes: z
set_position_z: 0
gcode:
    G90
    G0 Z5 F500
    G28 X0 Y0
    G0 X125 Y100 F9000
    G28 Z0
    G0 Z5 F500

#####################################################################
#     Bed/Mesh Stepper Tilt Settings
#####################################################################

[heater_bed]
heater_pin: PC8
sensor_type: ATC Semitec 104GT-2
# sensor_type: EPCOS 100K B57560G104F
sensor_pin: PC3
#control: watermark
min_temp: 0
max_temp: 130

[bed_mesh]
speed: 200
horizontal_move_z: 5
mesh_min: 25,35.0
mesh_max: 225.0,220
# probe_count: 6,6
probe_count: 5,5
algorithm: bicubic
fade_start: 1
fade_end: 10
fade_target: 0

[probe]
pin: ^PA0
x_offset: 0.0
y_offset: 25.0
#z_offset: -1.85
speed: 40

[screws_tilt_adjust]
# Screw 1 is considered the baseline
# For tilt adjust using SCREWS_TILT_CALCULATE
##
#         ******************
#         * S7    S8    S9 *
#         *                * 
#   Bed:  * S5    S1    S6 *  
#         *                *
#         * S2    S3    S4 *
#         ******************
#
screw1: 128,110
screw1_name: center
screw2: 18,5
screw2_name: front_left
screw3: 128,5
screw3_name: front_center
screw4: 233,5
screw4_name: front_right
screw5: 18,110
screw5_name: middle_left
screw6: 233,110
screw6_name: middle_right
screw7: 18,215
screw7_name: rear_left
screw8: 128,215
screw8_name: rear_center
screw9: 233,215
screw9_name: rear_right
speed: 200
screw_thread: CCW-M3

#####################################################################
#     Fans/Other Temps LED Stepper Settings
#####################################################################

#fan for printed model FAN0
[fan]
pin: PB1
# shutdown_speed: 1
# max_power: 1.0
# kick_start_time: 0.100

#tool fan for hotend FAN1
[heater_fan nozzle_fan]
pin: PB2
shutdown_speed: 1
max_power: 1.0
kick_start_time: 0.100
heater: extruder
heater_temp: 50.0
fan_speed: 1.0

#fan for control board FAN2
[heater_fan control_fan]
pin: PB0

[temperature_sensor chamber]
# sensor_type: NTC 100K beta 3950
sensor_type: Custom NTC100K B3950
sensor_pin: PC2
min_temp: 0
max_temp: 100
gcode_id: C

#*# <---------------------- SAVE_CONFIG ---------------------->
#*# DO NOT EDIT THIS BLOCK OR BELOW. The contents are auto-generated.
#*#
#*# [heater_bed]
#*# control = pid
#*# pid_kp = 61.223
#*# pid_ki = 0.865
#*# pid_kd = 1083.640
#*#
#*# [extruder]
#*# control = pid
#*# pid_kp = 32.825
#*# pid_ki = 1.683
#*# pid_kd = 160.023
#*#
#*# [probe]
#*# z_offset = 2.012
#*#
#*# [bed_mesh default]
#*# version = 1
#*# points =
#*# 	  -0.143750, -0.162500, -0.162500, -0.025000, 0.156250
#*# 	  -0.006250, -0.093750, -0.056250, -0.031250, 0.125000
#*# 	  -0.043750, -0.143750, 0.000000, -0.112500, 0.050000
#*# 	  0.037500, -0.018750, -0.012500, 0.050000, 0.206250
#*# 	  0.112500, -0.006250, -0.006250, 0.087500, 0.343750
#*# tension = 0.2
#*# min_x = 25.0
#*# algo = bicubic
#*# y_count = 5
#*# mesh_y_pps = 2
#*# min_y = 35.0
#*# x_count = 5
#*# max_y = 220.0
#*# mesh_x_pps = 2
#*# max_x = 225.0

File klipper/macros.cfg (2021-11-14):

[display_status]

[gcode_macro CANCEL_PRINT]
rename_existing: BASE_CANCEL_PRINT
gcode:
    M104 S0
    M140 S0
    M106 S0
    G91 E-2
    CLEAR_PAUSE
    BASE_CANCEL_PRINT
    Park_toolhead
    SDCARD_RESET_FILE
    M221 S100
    BED_MESH_CLEAR

[gcode_macro DISABLE_MOTORS]
gcode:
    M18

[gcode_macro HEATSOAK]
gcode:
    G4 P{params.DWELL}

[gcode_macro M600]
gcode:
    {% set X = params.X|default(50)|float %}
    {% set Y = params.Y|default(0)|float %}
    {% set Z = params.Z|default(10)|float %}
    SAVE_GCODE_STATE NAME=M600_state
    PAUSE
    G91 
    G1 E-.8 F2700
    G1 Z{Z}
    G90
    G1 X{X} Y{Y} F3000
    G91
    G1 E-50 F1000
    RESTORE_GCODE_STATE NAME=M600_state

[gcode_macro PAUSE]
rename_existing: BASE_PAUSE
gcode:
    #Edit this#
    {% set X = 230 %}
    {% set Y = 230 %}
    {% set Z = 10  %}
    ###########
    SAVE_GCODE_STATE NAME=PAUSE_state
    BASE_PAUSE
    G91
    G1 E-1.7 F2100
    G1 Z{Z}
    G90
    G1 X{X} Y{Y} F6000
    G91


[gcode_macro PRINT_END]
gcode:
    # Turn off bed, extruder, and fan
    M140 S0
    M104 S0
    M106 S0
    # Move nozzle away from print while retracting
    G91
    G1 E-0.5 F300
    G0 Z10
    # lights off
    SET_PIN PIN=caselight VALUE=0.00


[gcode_macro PRINT_START]
gcode:
    
    {% set extruderTemp = params.EXTRUDER|default(230)|int %}  # Extruder temperature, default is 230
    {% set bedTemp = params.BED|default(90)|int %}             # Heated bed temperature, default is 90
    {% set dwellTemp = params.DWELL|default(120000)|int %}     # Heatsoaking duration in miliseconds, default 2 minutes
    {% set chamberTemp = params.DWELL|default(30)|int %}       # Chamber temp to heat to, default 30 minutes

    # Loading extruder and bed temperature
    M104 S{extruderTemp|float*0.75}
    M140 S{bedTemp}
    
    M117  Waiting for temperatures...
    M190 S{bedTemp} # Wait for bed to come to temperature
    # RESPOND PREFIX= MSG="Waiting for thermal expansion..."
    M117 Waiting for thermal expansion...
    HEATSOAK DWELL={dwellTemp} # Dwelling
    
    # Homing and creating a mesh
    M117 Creating a mesh...
    G28
    BED_MESH_CALIBRATE
    M104 S{extruderTemp} # Set extruder to printing temperature

    # lights on, purge
    SET_PIN PIN=caselight VALUE=1.00
    PRIME_LINE

[gcode_macro PRIME_LINE]
gcode:
    SAVE_GCODE_STATE NAME=BEFORE_PRIME
    M117 Prime Line
    G0 X15.0 Y10.0 F5000.0  ; Go to X3 Y3
    G1 Z0.2 F200            ; Set nozzle height
    G92 E0.0                ; reset extrusion distance
    G1 X60.0 E9.0 F1000.0   ; intro line
    #G1 X100.0 E12.5 F1000.0 ; intro line
    G1 X100.0 E10 F1000.0 ; intro line
    G92 E0.0                ; reset extrusion distance
    G1 Z1 F5000             ; Lift Z
    RESTORE_GCODE_STATE NAME=BEFORE_PRIME  

[gcode_macro PURGE]
gcode:
    SAVE_GCODE_STATE NAME=BEFORE_PURGE
    M117 Purging
    G0 X2 Y2 F5000
    G91
    G1 E9 F500
    G90
    RESTORE_GCODE_STATE NAME=BEFORE_PURGE

[gcode_macro RESUME]
rename_existing: BASE_RESUME
gcode:
    G91
    G1 E1.7 F2100
    G91
    RESTORE_GCODE_STATE NAME=PAUSE_state MOVE=1
    BASE_RESUME

[gcode_macro Screws_tilt]
gcode:
    G28 #Home All Axes
    SCREWS_TILT_CALCULATE samples=3
    # G1 X{ home_x - probe_x_offset } Y230 Z200 F{ travel_speed }

[gcode_macro SEARCH_VARS]
gcode:
    {% set search = params.S|lower %}
    {% set ns = namespace() %}
    {% for item in printer  %}
        {% if ' ' in item %}
            {% set ns.path = ['printer', "['%s']" % (item), ''] %}
        {% else %}
            {% set ns.path = ['printer.', item, ''] %}   
        {% endif %} 

        {% if search in ns.path|lower %}
            { action_respond_info(ns.path|join) }
        {% endif %} 

        {% if printer[item].items() %}
            {% for childkey, child in printer[item].items() recursive %}
                {% set ns.path = ns.path[:loop.depth|int + 1] %}

                {% if ' ' in childkey %}
                    {% set null = ns.path.append("['%s']" % (childkey)) %}
                {% else %}
                    {% set null = ns.path.append(".%s" % (childkey)) %}
                {% endif %} 

                {% if child is mapping  %}
                    { loop(child.items()) }
                {% else %}
                    {% if search in ns.path|lower %}
                        { action_respond_info("%s : %s" % (ns.path|join, child)) }   
                    {% endif %} 
                {% endif %} 
                
            {% endfor %}
        {% endif %} 
    {% endfor %}

[gcode_macro TOGGLE_CASELIGHT]
gcode:
  SET_PIN PIN=caselight VALUE={(not printer['output_pin caselight'].value)|int}

[gcode_macro ZUP]
gcode:
    SET_GCODE_OFFSET Z_ADJUST=0.01 MOVE=1

[gcode_macro ZDOWN]
gcode:
    SET_GCODE_OFFSET Z_ADJUST=-0.01 MOVE=1


[pause_resume]

[virtual_sdcard]
path: ~/gcode_files

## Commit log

2021-08-15 updated readme, SW BOM
2021-09-08 updated materials list
    [Arduino_STM32F4xxVE.SchDoc, Low_MOS.SchDoc, Motor_Ctl.SchDoc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]
2021-11-06 serial request update
    [generic-fysetc-s6-v2.cfg, macros.cfg, macrosToAdd.cfg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]
2021-11-06 updated belts
2021-11-09 serial added
    [VS.287-NoLogo.stl, VS.287.stl]
2021-11-11 updated bat85 diode and motors
2021-11-14 updated config files
    [macros.cfg, printer.cfg]
